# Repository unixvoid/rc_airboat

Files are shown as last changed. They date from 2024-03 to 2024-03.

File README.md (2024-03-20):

Airboat
=======
<p align="center">
  
</p>
This project is an agile and speedy airboat designed with spare parts that I had laying around.  
Like most FPV pilots, I have a handfull of spare or broken parts laying around and I wanted to use on a watercraft design.
After countless testing and hull re-designing I finally landed on what I think is a good balanced hull design.
The hull is able to be taken up to full throttle and fully turned without capsizing or upsetting the hull too much.

This project is also posted to [thingiverse](https://www.thingiverse.com/thing:6541742 "thingiverse link")

Parts list:
===========
Here is the list of parts I used to create the airboat, but many other tinywhoop parts will work as well.

- Flight Controller: Happymodel Diamond F4 ELRS
- Motors: 2x newbeedrone 0703 16420kv
- Props: Gemfan 1610 biblade
- Battery: Betafpv 300mah bt2.0
- bit of velcro for battery strap
- conformal coating

How to print:
=============
This project is broken into 3 printable parts, You will need to print one of each of these pieces to complete your airboat.
I printed most of the hulls and the carrier in PLA with great success.  
I also tried out lightweight PLA on a couple hulls which ended up absorbing water, so I recommend other materials unless you want to coat it after printing.

### Hull


- This is the hull of the boat without any electronics or additional features  
- print upside down with supports touching buildplate)
- [airboat_neo_hull.stl](airboat_design/airboat_neo_hull.stl) can be found in the `airboat_design/` directory
---
### Carrier


- This is the model where all of the electronics are mounted, this can be moved to different hull designs  
- print flat side down with no supports 
- [carrier.stl](airboat_design/carrier.stl) can be found in the `airboat_design/` directory
---
### Carrier Plug


- This is a plug that fits in behind the carrier  
- it helps push the carrier forward to balance the weight on the hull and fills the gap behind the carrier
- Print large sizde down with no supports 
- [airboat_carrier_plug.stl](airboat_design/airboat_carrier_plug.stl) can be found in the `airboat_design/` directory

Programming FC:
===============
If you decided to use an old flight controller like I did, you'll need to configure it in betaflight to work as an airboat.
I have uploaded my [CLI dump](cli_dump/BF_airboat_diamondf4_dump.txt) if anyone is using a diamond f4, otherwise you'll need to do a few different configurations.

- Motor Resource allocation: You need to only enable the 2 motors that are being used.
  ```
  resource MOTOR 1 B07
  resource MOTOR 2 B10
  resource MOTOR 3 NONE
  resource MOTOR 4 NONE
  
  save
  ```

- Custom Motor Mixes: this will allow us to use a custom motor mix allowing us to turn using differential thrust
  ```
  mixer custom
  mmix reset
  mmix 0  1.000  0.000  0.000 -1.000
  mmix 1  1.000  0.000  0.000  1.000
  
  save
  ```

- Disable Profile Independant Filter Settings: We can disable much of the filtering since we aren't a quadcopter anymore.  
  - Disable `Gyro Lowpass Filters`, `Gyro Notch Filters`, and `Dynamic Notch Filter`  
  - [Reference photo](photos/airboat_bf_filters.png)

- Disable Runaway Prevention: On one of my boats, runaway prevention stopped me from hitting full power on the airboat, so I ended up disabling it
  ```
  set runaway_takeoff_prevention = OFF
  
  save
  ```

- Disable VTX: We need to disable the built in VTX if our FC has one so we dont cook the board. This can usually be accomplished by bridging a solder pad or disabling in software.  
  I have disabled the VTX in the `Configuration` -> `Other Features` tab in betaflight.

Extras:
=======
I've done extensive testing of different hulls, some of which lead to stranded vessels.
To recover vessels I'm testing out a floating recovery rope (floating fly fishing line) that I can pull behind one of the boat and "drive" the recovery boat+line around the stranded vessel to bring it home.
I have added the following miscellaneous parts to the project:

### Carrier Utility Plug
Airboat with utility setup

- The carrier plug can be swapped out with this Carrier Utility Plug to add a loop to the back of the airboat.
- [airboat_utility_plug.stl](airboat_design/airboat_utility_plug.stl) can be found in the `airboat_design/` directory
- print with no supports
---

I tested numerous hull designs looking for the most balanced. I even made a ramp boat so I can drive it out to the middle of the pond and ramp my other airboat. Turns out it had a tendency to capsize..
Here are some of my prototypes:
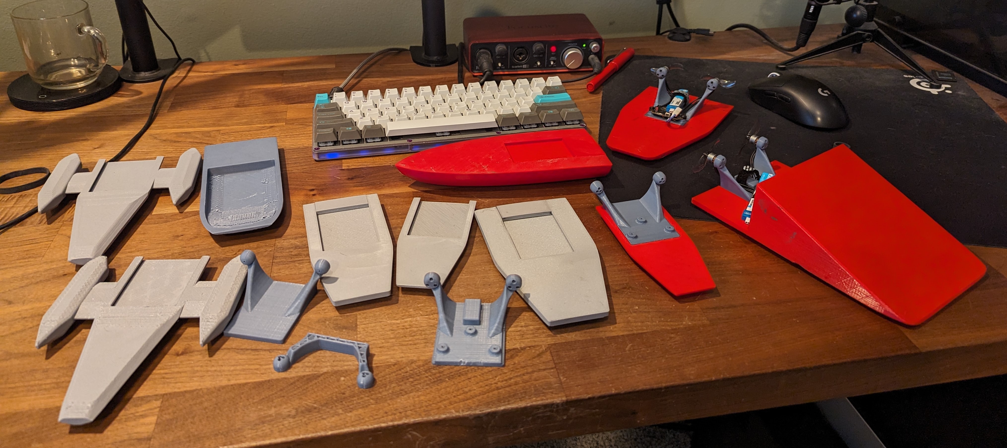
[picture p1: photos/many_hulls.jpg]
Many airboat hulls


If you've come this far, thanks for checking out my project, if you have any interest in the source files or to see all of my legacy designs, check out the project over on [onshape](https://cad.onshape.com/documents/6728372e51ea95be38f71059/w/a7f577bf32b5131d55028480/e/84ca7f1b91ac43509baaff38)

Indoor airboat testing (https://youtu.be/J2SFbNkRmbY)  
Airboat sea trials (https://youtu.be/VxDwH-HvI94)

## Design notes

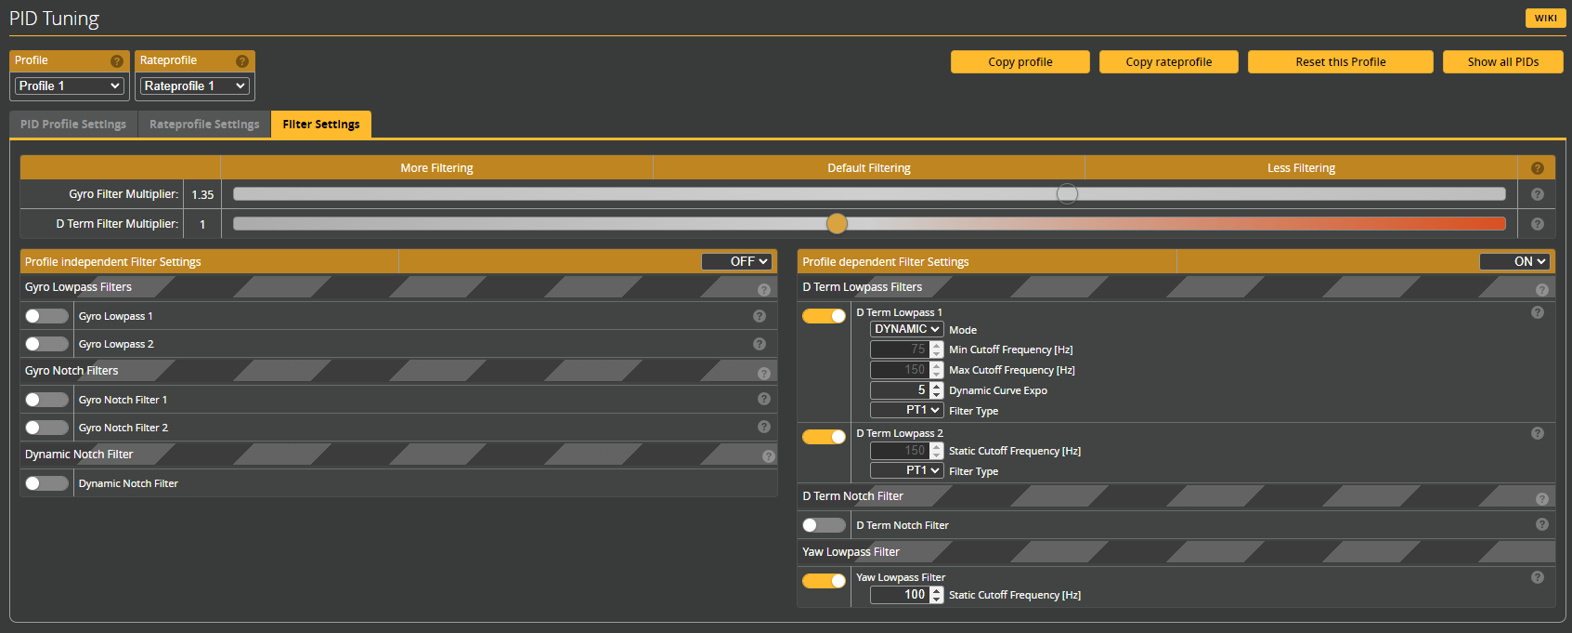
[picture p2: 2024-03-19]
photos/airboat_bf_filters.png

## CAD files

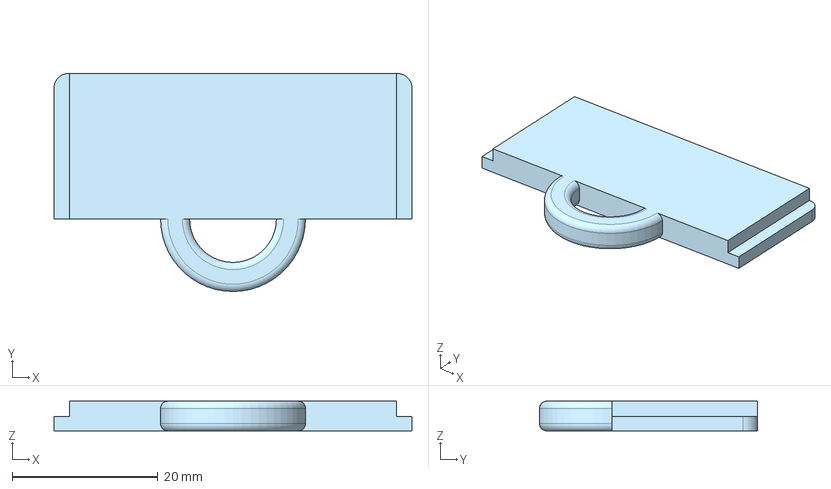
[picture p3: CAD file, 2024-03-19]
airboat_design/source/airboat_utility_plug.step
49.2 x 30.0 x 4.10 mm

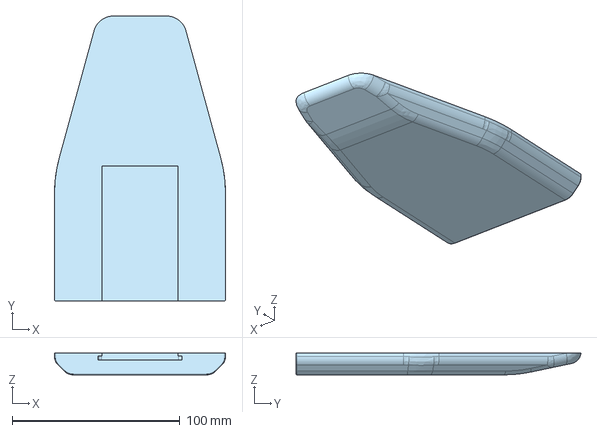
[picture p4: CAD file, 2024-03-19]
airboat_design/source/airboat_neo_hull.step
102.0 x 170.0 x 13.0 mm

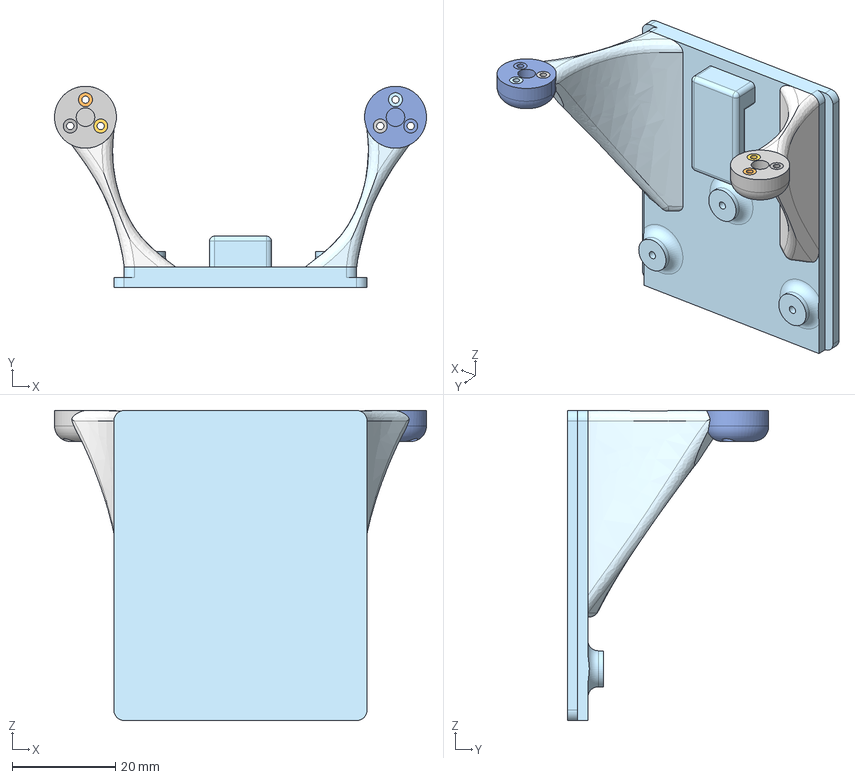
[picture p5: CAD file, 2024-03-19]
airboat_design/source/carrier.step
72.0 x 39.0 x 60.0 mm

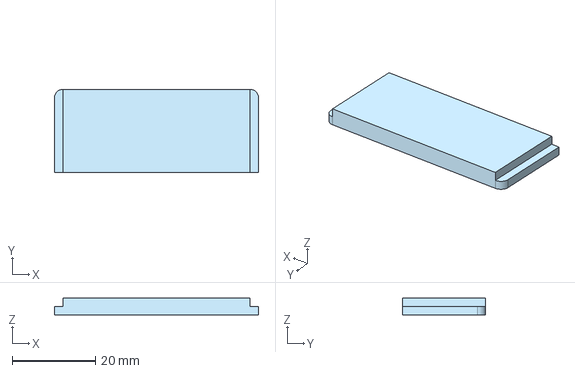
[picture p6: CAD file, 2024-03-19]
airboat_design/source/airboat_carrier_plug.step
49.0 x 20.0 x 4.00 mm

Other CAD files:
airboat_design/airboat_carrier_plug.stl
airboat_design/airboat_neo_hull.stl
airboat_design/airboat_utility_plug.stl
airboat_design/carrier.stl

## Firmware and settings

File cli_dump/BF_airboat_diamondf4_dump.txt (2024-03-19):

defaults nosave


# version
# Betaflight / STM32F411 (S411) 4.4.2 Dec 13 2023 / 07:05:27 (23d066d08) MSP API: 1.45

# config: YES

# start the command batch
batch start

# reset configuration to default settings
defaults nosave

board_name CRAZYBEEF4SX1280
manufacturer_id HAMO
mcu_id 004000143032510c33383735
signature 

# resources
resource MOTOR 1 B07
resource MOTOR 2 B10
resource MOTOR 3 NONE
resource MOTOR 4 NONE

# feature
feature -RX_SERIAL
feature -OSD
feature -AIRMODE
feature MOTOR_STOP
feature 3D
feature RX_SPI

# mixer
mixer CUSTOM
mmix 0  1.000  0.000  0.000 -1.000
mmix 1  1.000  0.000  0.000  1.000

# beacon
beacon RX_SET

# aux
aux 0 0 0 1950 2050 0 0

# master
set gyro_lpf1_static_hz = 0
set gyro_lpf2_static_hz = 0
set dyn_notch_count = 0
set gyro_lpf1_dyn_min_hz = 0
set gyro_lpf1_dyn_max_hz = 675
set acc_trim_pitch = -2
set acc_calibration = -77,31,66,1
set dshot_idle_value = 0
set motor_pwm_protocol = DSHOT300
set motor_output_reordering = 1,0,3,2,4,5,6,7
set vbat_max_cell_voltage = 440
set vbat_min_cell_voltage = 315
set vbat_warning_cell_voltage = 325
set 3d_deadband_low = 1450
set 3d_deadband_high = 1550
set 3d_neutral = 1500
set small_angle = 180
set pid_process_denom = 1
set runaway_takeoff_prevention = OFF
set simplified_gyro_filter = OFF
set simplified_gyro_filter_multiplier = 135
set vtx_band = 5
set vtx_channel = 8
set vtx_freq = 5917
set gyro_1_sensor_align = CW0FLIP
set gyro_1_align_pitch = 1800
set gyro_1_align_yaw = 0
set expresslrs_uid = changeme
set expresslrs_rate_index = 1

profile 0

# profile 0
set dterm_lpf1_dyn_min_hz = 0
set dterm_lpf1_dyn_max_hz = 202
set dterm_lpf1_static_hz = 0
set dterm_lpf2_static_hz = 0
set crash_recovery = ON
set yaw_lowpass_hz = 0
set p_yaw = 25
set i_yaw = 15
set simplified_pids_mode = RP
set simplified_dterm_filter = OFF
set simplified_dterm_filter_multiplier = 135

profile 1

profile 2

profile 3

# restore original profile selection
profile 0

rateprofile 0

# rateprofile 0
set rateprofile_name = squidx
set rates_type = BETAFLIGHT
set roll_rc_rate = 100
set pitch_rc_rate = 100
set yaw_rc_rate = 100
set roll_srate = 76
set pitch_srate = 76
set yaw_srate = 76

# restore original rateprofile selection
rateprofile 0

# save configuration

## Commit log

2024-03-19 Add stl and step files for hull, carrier, and plug
    [BF_airboat_diamondf4_dump.txt, airboat_carrier_plug.step, airboat_carrier_plug.stl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]
2024-03-19 Update cli dump
    [BF_airboat_diamondf4_dump.txt]
2024-03-19 Update readme with filter settings
2024-03-19 Move step files to new 'source' directory
    [airboat_carrier_plug.step, airboat_neo_hull.step, carrier.step]
2024-03-19 Add utility plug files Add many hulls image Update readme to reflect new files
    [airboat_utility_plug.step, airboat_utility_plug.stl]
